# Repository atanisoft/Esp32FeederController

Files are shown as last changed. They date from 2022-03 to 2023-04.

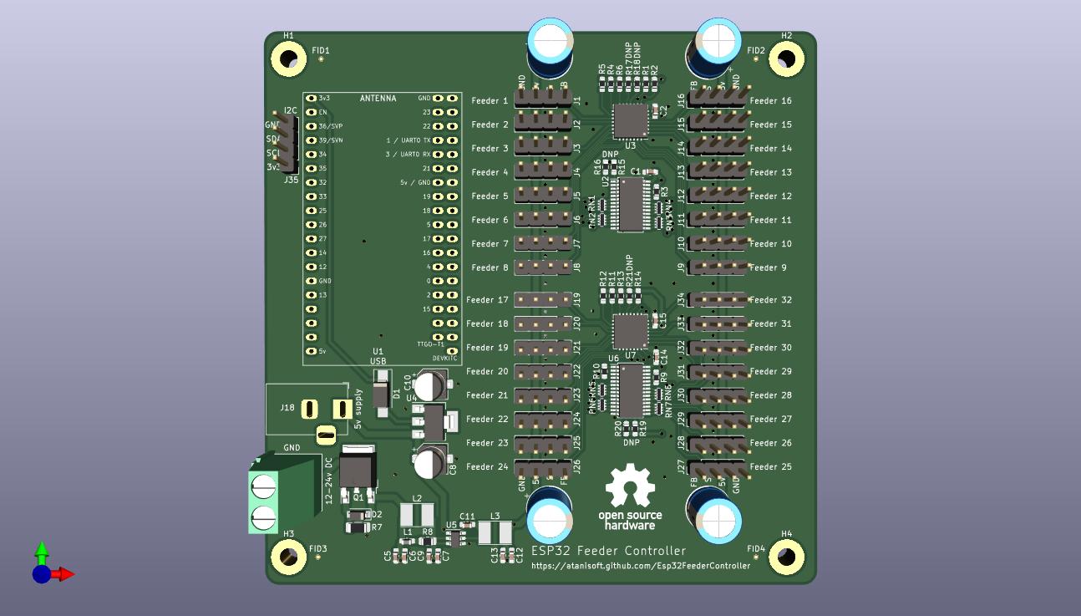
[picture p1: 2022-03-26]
pcb/FeederController.jpg

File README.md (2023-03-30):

# Esp32FeederController

The Esp32FeederController project allows controlling of multiple 0816 Feeders
using four wire cables.

## Supported Feeders

At this time the following feeder designs should work:

* [Original 0816 Feeder](https://docs.mgrl.de/maschine:pickandplace:feeder:0816feeder).
* [0816 Lumen Feeder](https://github.com/SupaCoder/0816-Lumen-SMT-Feeder-Remix).
* [Max Feeder](https://github.com/CurlyTaleGamesLLC/MAXFeederShield).

The [Max Feeder](https://github.com/CurlyTaleGamesLLC/MAXFeederShield) is the preferred
version of the feeder design as it supports adding a QR Code to the feeder that can be
used for automatic part identification.

### Feeder modifications / Addons

* [Reel holder](https://www.thingiverse.com/thing:3810696)
* [Vertical tape puller](https://github.com/SebG3D/TapePuller/wiki)

## Non-automatic feeders

* [Lumen Push/Pull Feeder](https://github.com/GatCode/LumenPPF)

# Adding Esp32FeederController to OpenPnP

Adding Esp32FeederController to OpenPnP consists of three steps:

* Create [GcodeDriver](https://github.com/openpnp/openpnp/wiki/GcodeDriver).
* Create [Actuators](https://github.com/openpnp/openpnp/wiki/Setup-and-Calibration%3A-Actuators) for Feeder actions.
* Create [Feeders](https://github.com/openpnp/openpnp/wiki/Setup-and-Calibration%3A-Feeders). 

### Creating the Gcode Driver

Each Esp32FeederController PCB should have it's own [GcodeDriver](https://github.com/openpnp/openpnp/wiki/GcodeDriver).

Steps to add a new [GcodeDriver](https://github.com/openpnp/openpnp/wiki/GcodeDriver) for Esp32FeederController:

* Navigate to the `Machine Setup` tab
* Traverse the list to the `Drivers` section, select and expand it.
* Click the `+` (add) icon and select `GcodeDriver`.
* Select the newly created `GcodeDriver GcodeDriver` entry.
* Set the `Name` so it can be easily identified later.
* Set `Communications Type` to `tcp`.
* Scroll down to the `TCP` section.
* Set `IP Address` based on the reported IP address in the serial output.
* Set `Port` to `8989`.
* Click the `Apply` button to save the updates.
* In the `File` menu select `Save Configuration` to ensure settings are not lost when restarting OpenPnP.

### Creating Actuators

Each Esp32FeederController PCB requires two `Actuators`:

* Feeder Advancement
* Feeder Post Pick

The following steps should be executed for the two `Actuators`:

* Navigate to the `Machine Setup` tab
* Traverse the list to the `Actuators` section, select and expand it.
* Click the `+` (add) icon and select `ReferenceActuator`.
* Select the newly created `ReferenceActuator ReferenceActuator` entry.
* Set `Driver` to the Esp32FeederController driver created previously.
* Set the `Name` so it can be easily identified later.
* Set `Value Type` to `Double`.
* Click the `Apply` button to save the updates.
* In the `File` menu select `Save Configuration` to ensure settings are not lost when restarting OpenPnP.

After the two `Actuators` have been defined it is necessary to configure the
Gcode commands to send for actuation, use the following steps to configure this:

* Navigate to the `Machine Setup` tab
* Traverse the list to the `Drivers` section, select and expand it.
* Click the `GcodeDriver Esp32FeederController` (or whatever name was provided previously).
* Navigate to the `Gcode` tab.
* In `Head Mountable` drop down select `Default`.
  * In `Setting` select `COMMAND_CONFIRM_REGEX` and enter `^ok.*`, be sure to click `Apply` before moving further.
  * In `Setting` select `COMMAND_ERROR_REGEX` and enter `^error.*`, be sure to click `Apply` before moving further.
* In `Head Mountable` drop down select `Actuator: [No Head] Feeder Advancement`.
  * In `Setting` select `ACTUATE_DOUBLE_COMMAND` and enter `M610 N{IntegerValue}*`, be sure to click `Apply` before moving further.
* In `Head Mountable` drop down select `Actuator: [No Head] Feeder Post Pick`.
  * In `Setting` select `ACTUATE_DOUBLE_COMMAND` and enter `M611 N{IntegerValue}*`, be sure to click `Apply` before moving further.
* In the `File` menu select `Save Configuration` to ensure settings are not lost when restarting OpenPnP.

## Configuring Feeders in OpenPnP

There are two types of feeders that will work well with Esp32FeederController:

* [ReferenceAutoFeeder](https://github.com/openpnp/openpnp/wiki/ReferenceAutoFeeder)
* [ReferenceSlotAutoFeeder](https://github.com/openpnp/openpnp/wiki/ReferenceSlotAutoFeeder)

Both operate similarly using the `Actuators` defined above.

* Navigate to the `Feeders` tab
* Click the `+` (add) icon and select `ReferenceAutoFeeder` or `ReferenceSlotAutoFeeder`.
* Select the newly created `ReferenceAutoFeeder ReferenceAutoFeeder` or `ReferenceSlotAutoFeeder ReferenceSlotAutoFeeder` entry.
* Double click on the newly created row in the `Name` column and rename it for easier identification.
* Set `Feed Actuator` to `Feeder Advancement` (or whichever name you provide the `Actuator`)
* Set `Post Pick Actuator` to `Feeder Post Pick` (or whichever name you provide the `Actuator`)
* Set `Actuator Value` on both `Actuators` to the feeder number on the Esp32FeederController PCB minus one (zero indexed).
* Click the `Apply` button to save the updates.
* In the `File` menu select `Save Configuration` to ensure settings are not lost when restarting OpenPnP.

Use the `Test Feed` and `Test post pick` to confirm the feeder is responding correctly.

## Supported Gcode commands

The Esp32FeederController supports multiple Gcode commands, many of which are
not directly used by OpenPnP. Many of the commands are intended to be used with
substitution of values within `{ }` marks, anything within `[ ]` are optional
arguments.

### Feeder Movement (M610)

`M610 N{feeder} [D{distance}]`

* `{feeder}` is the Feeder to be moved forward.
* `{distance}` is the distance to move the feeder and is optional.

### Feeder Post Pick (M611)

`M611 N{feeder}`

* `{feeder}` is the Feeder to be moved as part of post-pick.

### Feeder Status (M612)

`M612 N{feeder}`

* `{feeder}` is the Feeder to retrieve status for.

### Feeder Configuration (M613)

`M613 N{feeder} [A{advance angle}] [B{half advance angle}] [C{retract angle}] [D{degrees}] [F{feed length}] [S{speed}] [U{settle time}] [V{min pulse}] [W{max pulse}] [Z{feedback enabled}]`

All parameters except `{feeder}` are optional.

* `{feeder}` is the Feeder to be configured.
* `{advance angle}` is the angle to move the servo to for full extension.
* `{half advance angle}` is the angle to move the servo to for half extension.
* `{retract angle}` is the angle to move the servo to for retraction.
* `{degrees}` is the maximum number of degrees to move at one time, set to zero to move immediately.
* `{feed length}` is the number of millimeters (pitch) to move the feeder forward when moving to the next part and must be a multiple of 2.
* `{speed}` is the interval at which to move the servo between two angles, used in conjunction with `{degrees}`.
* `{settle time}` is the number of milliseconds to delay between servo movements.
* `{min pulse}` is the minimum number of pulses to send the servo.
* `{max pulse}` is the maximum number of pulses to send the servo.
* `{feedback enabled}` is used to enable or disable feedback checking as part of movement, set to zero to disable or one to enable

### Enable Feeder (M614)

`M614 N{feeder}`

* `{feeder}` is the Feeder to enable.

### Disable Feeder (M615)

`M615 N{feeder}`

* `{feeder}` is the Feeder to disable.

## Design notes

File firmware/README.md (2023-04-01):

# Esp32FeederController Firmware

The Esp32FeederController is built using two PCA9685 PWM generators and two
MCP23017 IO Expander ICs. The [custom PCB](../pcb/FeederController/) allows
control of up to 32 feeders with a single PCB.

## Configuring your build environment

Esp32FeederController is built using [ESP-IDF](https://github.com/espressif/esp-idf),
most testing is done with the master branch (v5.0 or later).
Please follow [these](https://docs.espressif.com/projects/esp-idf/en/latest/esp32/get-started/index.html#installation)
instructions for setting up your build environment.

## Building and flashing the firmware

Once the environment has been setup you are almost ready to build and upload the
binary to the ESP32. Before building you will need to configure your WiFi access
details in `firmware/main/config.hxx` in the `WIFI_SSID` and `WIFI_PASSWORD`
fields. Once the two WiFi fields have been updated you are ready to build.

Plug in the ESP32 to your computer and execute the following commands to build
and flash the firmware to the ESP32:

```
idf.py build flash monitor -p /dev/ttyUSB0
```

Adjust `/dev/ttyUSB0` to match the port assigned to the ESP32 when it is plugged
into your computer.

Once the firmware has been uploaded the ESP32 will restart and the serial output
will be displayed in the terminal. The startup process should take 5-10 seconds
the first time and will display the assigned IP address:

```
I (587) main: Initializing NVS
I (650) wifi_mgr: Setting hostname to "esp32feeder".
I (656) wifi_mgr: Configuring Station (SSID:YourWiFiNetwork)
I (657) wifi_mgr: Starting WiFi stack
I (756) wifi_mgr: WiFi station started.
I (1935) wifi_mgr: Connected to SSID:YourWiFiNetwork
I (1936) wifi_mgr: [1/36] Waiting for IP address assignment.
I (2104) wifi_mgr: IP address:10.0.0.13
I (2105) wifi_mgr: [2/36] Waiting for IP address assignment.
I (2114) gcode_server: Waiting for connections on 10.0.0.13:8989...
```
Make note of the IP address that is reported as you will need it for OpenPnP
configuration.

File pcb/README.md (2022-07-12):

# Custom PCBs

This tree contains custom PCBs for the Esp32FeederController. Note that this PCB
has not been extensively tested or verified to be bug-free. Please report any
issues with the PCBs and if possible a PR to correct them.

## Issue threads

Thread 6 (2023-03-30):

ESP32 abort on FeederManager.cpp

indexdb, 2023-03-30:
I use one PCA9685 and one MCP23017, ESP32 detected them, but reboot endless, please check log attached.

ESP32 abort on this line in FeederManager.cpp, then reboot ....
feeders_.push_back( std::make_shared<Feeder>(idx + 1, uuid, pca9685_[expander_index],
                                        mcp23017_[expander_index],
                                        expander_channel, context));

========================== LOG =================================
20:11:48.220 -> ELF file SHA256: 8720b8c32e64e776
20:11:48.220 ->
20:11:48.220 -> Rebooting...
20:11:48.220 -> ets Jun  8 2016 00:22:57
20:11:48.267 ->
20:11:48.267 -> rst:0xc (SW_CPU_RESET),boot:0x13 (SPI_FAST_FLASH_BOOT)
20:11:48.267 -> configsip: 0, SPIWP:0xee
20:11:48.267 -> clk_drv:0x00,q_drv:0x00,d_drv:0x00,cs0_drv:0x00,hd_drv:0x00,wp_drv:0x00
20:11:48.267 -> mode:DIO, clock div:2
20:11:48.267 -> load:0x3fff0030,len:6948
20:11:48.267 -> load:0x40078000,len:15500
20:11:48.267 -> load:0x40080400,len:3844
20:11:48.267 -> entry 0x4008064c
20:11:48.267 ->  [0;32mI (27) boot: ESP-IDF -128-NOTFOUND 2nd stage bootloader [0m
20:11:48.267 ->  [0;32mI (27) boot: compile time 16:58:17 [0m
20:11:48.267 ->  [0;32mI (27) boot: chip revision: v1.0 [0m
20:11:48.267 ->  [0;32mI (31) boot.esp32: SPI Speed      : 40MHz [0m
20:11:48.267 ->  [0;32mI (35) boot.esp32: SPI Mode       : DIO [0m
20:11:48.313 ->  [0;32mI (40) boot.esp32: SPI Flash Size : 4MB [0m
20:11:48.313 ->  [0;32mI (44) boot: Enabling RNG early entropy source... [0m
20:11:48.313 ->  [0;32mI (50) boot: Partition Table: [0m
20:11:48.313 ->  [0;32mI (53) boot: ## Label            Usage          Type ST Offset   Length [0m
20:11:48.313 ->  [0;32mI (61) boot:  0 nvs              WiFi data        01 02 00009000 00006000 [0m
20:11:48.313 ->  [0;32mI (68) boot:  1 phy_init         RF data          01 01 0000f000 00001000 [0m
20:11:48.313 ->  [0;32mI (76) boot:  2 factory          factory app      00 00 00010000 00177000 [0m
20:11:48.313 ->  [0;32mI (83) boot: End of partition table [0m
20:11:48.361 ->  [0;32mI (87) esp_image: segment 0: paddr=00010020 vaddr=3f400020 size=41804h (268292) map [0m
20:11:48.454 ->  [0;32mI (193) esp_image: segment 1: paddr=0005182c vaddr=3ffb0000 size=03638h ( 13880) load [0m
20:11:48.454 ->  [0;32mI (198) esp_image: segment 2: paddr=00054e6c vaddr=40080000 size=0b1ach ( 45484) load [0m
20:11:48.454 ->  [0;32mI (217) esp_image: segment 3: paddr=00060020 vaddr=400d0020 size=c53dch (807900) map [0m
20:11:48.735 ->  [0;32mI (509) esp_image: segment 4: paddr=00125404 vaddr=4008b1ac size=0b744h ( 46916) load [0m
20:11:48.782 ->  [0;32mI (540) boot: Loaded app from partition at offset 0x10000 [0m
20:11:48.782 ->  [0;32mI (540) boot: Disabling RNG early entropy source... [0m
20:11:48.829 ->  [0;32mI (567) main: Esp32FeederController 1 Initializing [0m
20:11:48.829 ->  [0;32mI (568) main: Compiled on Mar 28 2023 16:56:01 using IDF -128-NOTFOUND [0m
20:11:48.829 ->  [0;32mI (569) main: Running from: factory [0m
20:11:48.829 ->  [0;32mI (574) soc_info: Reset reason:software reset (CPU) (12), model:ESP32, chip revision:100, number of cores:2, embedded flash:No, embedded PSRAM: No, WiFi:Yes, IEEE 802.15.4:No, BLE:Yes, BT:Yes [0m
20:11:48.829 ->  [0;32mI (591) main: Initializing NVS [0m
20:11:48.875 ->  [0;32mI (626) wifi_mgr: Setting hostname to "esp32feeder". [0m
20:11:48.875 ->  [0;32mI (632) wifi_mgr: Configuring Station (SSID:QiQi Wifi-2.4G) [0m
20:11:48.875 ->  [0;32mI (633) wifi_mgr: Starting WiFi stack [0m
20:11:48.969 ->  [0;32mI (723) wifi_mgr: WiFi station started. [0m
20:11:49.579 -> E (1328) wifi:Association refused temporarily, comeback time 1004 mSec
20:11:50.562 -> E (2339) wifi:Association refused temporarily, comeback time 1004 mSec
20:11:51.590 ->  [0;32mI (3349) wifi_mgr: Connection to SSID:QiQi Wifi-2.4G (reason:203) failed [0m
20:11:51.636 ->  [0;32mI (3386) wifi_mgr: Connected to SSID:QiQi Wifi-2.4G [0m
20:11:51.636 ->  [0;32mI (3387) wifi_mgr: [1/36] Waiting for IP address assignment. [0m
20:11:52.622 ->  [0;32mI (4388) wifi_mgr: IP address:192.168.1.164 [0m
20:11:52.622 ->  [0;32mI (4389) wifi_mgr: [2/36] Waiting for IP address assignment. [0m
20:11:52.622 ->  [0;32mI (4397) gcode_client_mgr: 0 clients connected [0m
20:11:52.669 ->  [0;32mI (4399) gcode_server: Waiting for connections on 192.168.1.164:8989... [0m
20:11:52.669 ->  [0;32mI (4406) feeder_mgr: Initializing I2C Bus [0m
20:11:52.669 ->  [0;33mW (4408) feeder_mgr: PCA9685(40) was not detected. [0m
20:11:52.669 ->  [0;33mW (4412) feeder_mgr: PCA9685(41) was not detected. [0m
20:11:52.669 ->  [0;33mW (4418) feeder_mgr: PCA9685(42) was not detected. [0m
20:11:52.669 ->  [0;32mI (4425) feeder_mgr: PCA9685(43/0x3ffca244) configured for use. [0m
20:11:52.669 ->  [0;33mW (4430) feeder_mgr: PCA9685(44) was not detected. [0m
20:11:52.669 ->  [0;33mW (4435) feeder_mgr: PCA9685(45) was not detected. [0m
20:11:52.717 ->  [0;33mW (4441) feeder_mgr: PCA9685(46) was not detected. [0m
20:11:52.717 ->  [0;33mW (4446) feeder_mgr: PCA9685(47) was not detected. [0m
20:11:52.717 ->  [0;32mI (4451) feeder_mgr: Detected PCA9685 devices:1 [0m
20:11:52.717 ->  [0;33mW (4457) feeder_mgr: MCP23017(20) was not detected! [0m
20:11:52.717 ->  [0;33mW (4462) feeder_mgr: MCP23017(21) was not detected! [0m
20:11:52.717 ->  [0;33mW (4468) feeder_mgr: MCP23017(22) was not detected! [0m
20:11:52.717 ->  [0;32mI (4477) feeder_mgr: MCP23017(23/0x3ffca284) configured for use. [0m
20:11:52.717 ->  [0;33mW (4480) feeder_mgr: MCP23017(24) was not detected! [0m
20:11:52.717 ->  [0;33mW (4486) feeder_mgr: MCP23017(25) was not detected! [0m
20:11:52.765 ->  [0;33mW (4491) feeder_mgr: MCP23017(26) was not detected! [0m
20:11:52.765 ->  [0;33mW (4497) feeder_mgr: MCP23017(27) was not detected! [0m
20:11:52.765 ->
20:11:52.765 -> abort() was called at PC 0x4014f40f on core 0
20:11:52.765 ->
20:11:52.765 ->
20:11:52.765 -> Backtrace: 0x40081f0e:0x3ffba1c0 0x40089eed:0x3ffba1e0 0x40090f22:0x3ffba200 0x4014f40f:0x3ffba280 0x4014f444:0x3ffba2a0 0x4014f51f:0x3ffba2c0 0x400e35cb:0x3ffba2e0 0x400e0c9e:0x3ffba360 0x400dab79:0x3ffba610 0x40193669:0x3ffba7a0 0x4008d331:0x3ffba7c0
20:11:52.813 ->
20:11:52.813 ->
20:11:52.813 ->
20:11:52.813 ->

atanisoft, 2023-03-30:
Can you provide the full decode of the backtrace? Also what version of ESP-IDF did you use?
```
20:11:48.267 -> �[0;32mI (27) boot: ESP-IDF -128-NOTFOUND 2nd stage bootloader�[0m
...
20:11:48.829 -> �[0;32mI (567) main: Esp32FeederController 1 Initializing�[0m
20:11:48.829 -> �[0;32mI (568) main: Compiled on Mar 28 2023 16:56:01 using IDF -128-NOTFOUND�[0m
```
These lines normally should have the ESP-IDF version but they are showing up as an invalid version. So I'm not sure how you built this thus the questions.

indexdb, 2023-03-30:
please check new log as follow
=======================
I (27) boot: ESP-IDF v5.0.1-dirty 2nd stage bootloader
I (27) boot: compile time 09:39:36
I (27) boot: chip revision: v1.0
I (31) boot.esp32: SPI Speed      : 40MHz
I (35) boot.esp32: SPI Mode       : DIO
I (40) boot.esp32: SPI Flash Size : 4MB
I (44) boot: Enabling RNG early entropy source...
I (50) boot: Partition Table:
I (53) boot: ## Label            Usage          Type ST Offset   Length
I (61) boot:  0 nvs              WiFi data        01 02 00009000 00006000
I (68) boot:  1 phy_init         RF data          01 01 0000f000 00001000
I (76) boot:  2 factory          factory app      00 00 00010000 00177000
I (83) boot: End of partition table
I (87) esp_image: segment 0: paddr=00010020 vaddr=3f400020 size=4145ch (267356) map
I (192) esp_image: segment 1: paddr=00051484 vaddr=3ffb0000 size=03638h ( 13880) load
I (198) esp_image: segment 2: paddr=00054ac4 vaddr=40080000 size=0b554h ( 46420) load
I (217) esp_image: segment 3: paddr=00060020 vaddr=400d0020 size=c498ch (805260) map
I (508) esp_image: segment 4: paddr=001249b4 vaddr=4008b554 size=0b32ch ( 45868) load
I (539) boot: Loaded app from partition at offset 0x10000
I (539) boot: Disabling RNG early entropy source...
I (566) main: Esp32FeederController 1 Initializing
I (567) main: Compiled on Mar 30 2023 09:35:52 using IDF v5.0.1-dirty
I (568) main: Running from: factory
I (572) soc_info: Reset reason:software reset (CPU) (12), model:ESP32, chip revision:100, number of cores:2, embedded flash:No, embedded PSRAM: No, WiFi:Yes, IEEE 802.15.4:No, BLE:Yes, BT:Yes
I (590) main: Initializing NVS
I (623) wifi_mgr: Setting hostname to "esp32feeder".
I (630) wifi_mgr: Configuring Station (SSID:QiQi Wifi-2.4G)
I (630) wifi_mgr: Starting WiFi stack
I (721) wifi_mgr: WiFi station started.
I (1759) wifi_mgr: Connected to SSID:XXXXX
I (1760) wifi_mgr: [1/36] Waiting for IP address assignment.
I (1773) wifi_mgr: IP address:192.168.1.164
I (1773) wifi_mgr: [2/36] Waiting for IP address assignment.
I (1781) gcode_client_mgr: 0 clients connected
I (1782) gcode_server: Waiting for connections on 192.168.1.164:8989...
I (1790) feeder_mgr: Initializing I2C Bus
W (1792) feeder_mgr: PCA9685(40) was not detected.
W (1796) feeder_mgr: PCA9685(41) was not detected.
W (1802) feeder_mgr: PCA9685(42) was not detected.
I (1809) feeder_mgr: PCA9685(43/0x3ffca198) configured for use.
W (1814) feeder_mgr: PCA9685(44) was not detected.
W (1819) feeder_mgr: PCA9685(45) was not detected.
W (1825) feeder_mgr: PCA9685(46) was not detected.
W (1830) feeder_mgr: PCA9685(47) was not detected.
I (1838) feeder_mgr: Detected PCA9685 devices:1
W (1841) feeder_mgr: MCP23017(20) was not detected!
W (1847) feeder_mgr: MCP23017(21) was not detected!
W (1853) feeder_mgr: MCP23017(22) was not detected!
I (1861) feeder_mgr: MCP23017(23/0x3ffca1d8) configured for use.
W (1864) feeder_mgr: MCP23017(24) was not detected!
W (1870) feeder_mgr: MCP23017(25) was not detected!
W (1875) feeder_mgr: MCP23017(26) was not detected!
W (1881) feeder_mgr: MCP23017(27) was not detected!

abort() was called at PC 0x4014eab3 on core 0
0x4014eab3: __cxxabiv1::__terminate(void (*)()) at /builds/idf/crosstool-NG/.build/HOST-x86_64-w64-mingw32/xtensa-esp32-elf/src/gcc/libstdc++-v3/libsupc++/eh_terminate.cc:48
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
atanisoft, 2023-03-30:
Thanks for reproducing it on IDF v4.4. This was working previously and was tested, something must have changed in the gcc versions or IDF since I last tested this.

I'm working on adding some additional logging and support fixes for IDF v5+. Did you see this sort of failure in your testing?
```
xtensa-esp32-elf/bin/ld: esp-idf/espressif__asio/libespressif__asio.a(asio.cpp.obj):(.literal._ZN4asio6detail10socket_ops9inet_ntopEiPKvPcjmRSt10error_code+0x8): undefined reference to `if_indextoname'
xtensa-esp32-elf/bin/ld: esp-idf/espressif__asio/libespressif__asio.a(asio.cpp.obj): in function `_ZN4asio6detail10socket_ops9inet_ntopEiPKvPcjmRSt10error_code':
Esp32FeederController/firmware/managed_components/espressif__asio/asio/asio/include/asio/detail/impl/socket_ops.ipp:2128: undefined reference to `if_indextoname'
collect2: error: ld returned 1 exit status
```

indexdb, 2023-03-30:
Yes，I see that failure and I fix it by adding
----------------------------------------------------------
char* if_indextoname(unsigned int , char* ) { return 0; }
----------------------------------------------------------
to file socket_ops.ipp

You can check the link for this issue
https://github.com/espressif/esp-idf/issues/3557

atanisoft, 2023-03-30:
That was fixed and should have been included in the latest IDF but something is broken on asio it seems still. I saw a PR adding a missing header reference for the same thing. I'll be adding the weak function definition as referenced from that issue in my update.

atanisoft, 2023-03-30:
@indexdb Can you test the code on "idfv5" branch? It should compile cleanly without needing to alter anything with IDF v5.0.x

indexdb, 2023-03-30:
Yes, it works， Thank you！

Closed 2023-03-30.

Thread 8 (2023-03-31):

GCode command return nothing

indexdb, 2023-03-31:
I try to send Gcode command （ex. M115）from openpnp gcode driver console，got nothing.
Sometimes it returns "ok", most of the time it returns nothing
-----------------------------------------------------------------------
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
ok
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
-----------------------------------------------------------------------------
I (27) boot: ESP-IDF v5.0.1-dirty 2nd stage bootloader
I (27) boot: compile time 19:27:32
I (27) boot: chip revision: v1.0
I (30) boot.esp32: SPI Speed      : 40MHz
I (35) boot.esp32: SPI Mode       : DIO
I (39) boot.esp32: SPI Flash Size : 4MB
I (44) boot: Enabling RNG early entropy source...
I (49) boot: Partition Table:
I (53) boot: ## Label            Usage          Type ST Offset   Length
I (60) boot:  0 nvs              WiFi data        01 02 00009000 00006000
I (68) boot:  1 phy_init         RF data          01 01 0000f000 00001000
I (75) boot:  2 factory          factory app      00 00 00010000 00177000
I (83) boot: End of partition table
I (87) esp_image: segment 0: paddr=00010020 vaddr=3f400020 size=4163ch (267836) map
I (192) esp_image: segment 1: paddr=00051664 vaddr=3ffb0000 size=03638h ( 13880) load
I (198) esp_image: segment 2: paddr=00054ca4 vaddr=40080000 size=0b374h ( 45940) load
I (217) esp_image: segment 3: paddr=00060020 vaddr=400d0020 size=c4b88h (805768) map
I (508) esp_image: segment 4: paddr=00124bb0 vaddr=4008b374 size=0b50ch ( 46348) load
I (539) boot: Loaded app from partition at offset 0x10000
I (539) boot: Disabling RNG early entropy source...
I (566) main: Esp32FeederController 1 Initializing
I (567) main: Compiled on Mar 31 2023 19:23:37 using IDF v5.0.1-dirty
I (568) main: Running from: factory
I (572) soc_info: Reset reason:power on reset (1), model:ESP32, chip revision:100, number of cores:2, embedded flash:No, embedded PSRAM: No, WiFi:Yes, IEEE 802.15.4:No, BLE:Yes, BT:Yes
I (590) main: Initializing NVS
I (623) wifi_mgr: Setting hostname to "esp32feeder".
I (630) wifi_mgr: Configuring Station (SSID: Wifi-2.4G)
I (630) wifi_mgr: Starting WiFi stack
I (720) wifi_mgr: WiFi station started.
I (1971) wifi_mgr: Connected to SSID: Wifi-2.4G
I (1972) wifi_mgr: [1/36] Waiting for IP address assignment.
I (1996) wifi_mgr: IP address:192.168.1.164
I (1997) wifi_mgr: [2/36] Waiting for IP address assignment.
I (2004) gcode_client_mgr: 0 clients connected
I (2005) gcode_server: Waiting for connections on 192.168.1.164:8989...
I (2013) feeder_mgr: Initializing I2C Bus
W (2015) feeder_mgr: PCA9685(40) was not detected.
W (2019) feeder_mgr: PCA9685(41) was not detected.
W (2025) feeder_mgr: PCA9685(42) was not detected.
I (2032) feeder_mgr: PCA9685(43/0x3ffca198) configured for use.
W (2037) feeder_mgr: PCA9685(44) was not detected.
W (2042) feeder_mgr: PCA9685(45) was not detected.
W (2048) feeder_mgr: PCA9685(46) was not detected.
W (2053) feeder_mgr: PCA9685(47) was not detected.
I (2059) feeder_mgr: Detected PCA9685 devices:1
W (2064) feeder_mgr: MCP23017(20) was not detected!
W (2070) feeder_mgr: MCP23017(21) was not detected!
W (2076) feeder_mgr: MCP23017(22) was not detected!
I (2085) feeder_mgr: MCP23017(23/0x3ffca1d8) configured for use.
W (2088) feeder_mgr: MCP23017(24) was not detected!
W (2093) feeder_mgr: MCP23017(25) was not detected!
W (2099) feeder_mgr: MCP23017(26) was not detected!
W (2104) feeder_mgr: MCP23017(27) was not detected!
I (2109) feeder_mgr: Attempting to create 16 feeders
I (2115) feeder_mgr: Detected 1 PCA9685 and 1 MCP23017
I (2121) feeder_mgr: Creating feeder A593131F (1/0/0/PCA:0x3ffca198/MCP:0x3ffca1d8)
I (2131) feeder: [A593131F:1] Initializing using PCA9685 0x3ffca198:0
I (2136) PCA9685: [43:0] Moving to 15 deg
I (2142) feeder_mgr: Enabling feeder A593131F (1)
I (2147) feeder_mgr: Creating feeder 97F4FAD4 (2/0/1/PCA:0x3ffca198/MCP:0x3ffca1d8)
I (2156) feeder: [97F4FAD4:2] Initializing using PCA9685 0x3ffca198:1
I (2162) PCA9685: [43:1] Moving to 15 deg
I (2168) feeder_mgr: Enabling feeder 97F4FAD4 (2)
I (2172) feeder_mgr: Creating feeder 0E638528 (3/0/2/PCA:0x3ffca198/MCP:0x3ffca1d8)
I (2183) feeder: [0E638528:3] Initializing using PCA9685 0x3ffca198:2
I (2187) PCA9685: [43:2] Moving to 15 deg
I (2193) feeder_mgr: Enabling feeder 0E638528 (3)
I (2198) feeder_mgr: Creating feeder D3C5EB5D (4/0/3/PCA:0x3ffca198/MCP:0x3ffca1d8)
I (2207) feeder: [D3C5EB5D:4] Initializing using PCA9685 0x3ffca198:3
I (2213) PCA9685: [43:3] Moving to 15 deg
I (2219) feeder_mgr: Enabling feeder D3C5EB5D (4)
I (2223) feeder_mgr: Creating feeder 775C7838 (5/0/4/PCA:0x3ffca198/MCP:0x3ffca1d8)
I (2233) feeder: [775C7838:5] Initializing using PCA9685 0x3ffca198:4
I (2238) PCA9685: [43:4] Moving to 15 deg
I (2244) feeder_mgr: Enabling feeder 775C7838 (5)
I (2249) feeder_mgr: Creating feeder 660C64E1 (6/0/5/PCA:0x3ffca198/MCP:0x3ffca1d8)
I (2258) feeder: [660C64E1:6] Initializing using PCA9685 0x3ffca198:5
I (2264) PCA9685: [43:5] Moving to 15 deg
I (2270) feeder_mgr: Enabling feeder 660C64E1 (6)
I (2274) feeder_mgr: Creating feeder 6134C54A (7/0/6/PCA:0x3ffca198/MCP:0x3ffca1d8)
I (2284) feeder: [6134C54A:7] Initializing using PCA9685 0x3ffca198:6
I (2290) PCA9685: [43:6] Moving to 15 deg
I (2296) feeder_mgr: Enabling feeder 6134C54A (7)
I (2300) feeder_mgr: Creating feeder D037A224 (8/0/7/PCA:0x3ffca198/MCP:0x3ffca1d8)
I (2310) feeder: [D037A224:8] Initializing using PCA9685 0x3ffca198:7
I (2315) PCA9685: [43:7] Moving to 15 deg
I (2321) feeder_mgr: Enabling feeder D037A224 (8)
I (2325) feeder_mgr: Creating feeder E351A565 (9/0/8/PCA:0x3ffca198/MCP:0x3ffca1d8)
I (2335) feeder: [E351A565:9] Initializing using PCA9685 0x3ffca198:8
I (2341) PCA9685: [43:8] Moving to 15 deg
I (2346) feeder_mgr: Enabling feeder E351A565 (9)
I (2351) feeder_mgr: Creating feeder AF13AC02 (10/0/9/PCA:0x3ffca198/MCP:0x3ffca1d8)
I (2360) feeder: [AF13AC02:10] Initializing using PCA9685 0x3ffca198:9
I (2366) PCA9685: [43:9] Moving to 15 deg
I (2372) feeder_mgr: Enabling feeder AF13AC02 (10)
I (2376) feeder_mgr: Creating feeder C06BE9EC (11/0/10/PCA:0x3ffca198/MCP:0x3ffca1d8)
I (2388) feeder: [C06BE9EC:11] Initializing using PCA9685 0x3ffca198:10
I (2392) PCA9685: [43:10] Moving to 15 deg
I (2398) feeder_mgr: Enabling feeder C06BE9EC (11)
I (2402) feeder_mgr: Creating feeder 97FBF52B (12/0/11/PCA:0x3ffca198/MCP:0x3ffca1d8)
I (2413) feeder: [97FBF52B:12] Initializing using PCA9685 0x3ffca198:11
I (2418) PCA9685: [43:11] Moving to 15 deg
I (2424) feeder_mgr: Enabling feeder 97FBF52B (12)
I (2428) feeder_mgr: Creating feeder 67703760 (13/0/12/PCA:0x3ffca198/MCP:0x3ffca1d8)
I (2438) feeder: [67703760:13] Initializing using PCA9685 0x3ffca198:12
I (2444) PCA9685: [43:12] Moving to 15 deg
I (2450) feeder_mgr: Enabling feeder 67703760 (13)
I (2455) feeder_mgr: Creating feeder E8631392 (14/0/13/PCA:0x3ffca198/MCP:0x3ffca1d8)
I (2464) feeder: [E8631392:14] Initializing using PCA9685 0x3ffca198:13
I (2470) PCA9685: [43:13] Moving to 15 deg
I (2476) feeder_mgr: Enabling feeder E8631392 (14)
I (2481) feeder_mgr: Creating feeder E838AF2F (15/0/14/PCA:0x3ffca198/MCP:0x3ffca1d8)
I (2491) feeder: [E838AF2F:15] Initializing using PCA9685 0x3ffca198:14
I (2496) PCA9685: [43:14] Moving to 15 deg
I (2502) feeder_mgr: Enabling feeder E838AF2F (15)
I (2507) feeder_mgr: Creating feeder 5CB0F53D (16/0/15/PCA:0x3ffca198/MCP:0x3ffca1d8)
I (2517) feeder: [5CB0F53D:16] Initializing using PCA9685 0x3ffca198:15
I (2522) PCA9685: [43:15] Moving to 15 deg
I (2528) feeder_mgr: Enabling feeder 5CB0F53D (16)
I (2533) feeder_mgr: Configured Feeders:16
I (2538) heap_mon: Heap: 241.09kB / 328.48kB
I (2543) main: Creating 4 worker threads
I (2551) feeder: [A593131F:1] Feeder movement complete, turning off servo
I (2551) feeder: [97F4FAD4:2] Feeder movement complete, turning off servo
I (2551) feeder: [0E638528:3] Feeder movement complete, turning off servo
I (2552) feeder: [D3C5EB5D:4] Feeder movement complete, turning off servo
I (2556) feeder: [775C7838:5] Feeder movement complete, turning off servo
I (2564) feeder: [660C64E1:6] Feeder movement complete, turning off servo
I (2570) feeder: [6134C54A:7] Feeder movement complete, turning off servo
I (2581) feeder: [D037A224:8] Feeder movement complete, turning off servo
I (2588) feeder: [E351A565:9] Feeder movement complete, turning off servo
I (2614) feeder: [AF13AC02:10] Feeder movement complete, turning off servo
I (2552) main: Esp32FeederController Ready!
I (2640) feeder: [C06BE9EC:11] Feeder movement complete, turning off servo
I (2665) feeder: [97FBF52B:12] Feeder movement complete, turning off servo
I (2692) feeder: [67703760:13] Feeder movement complete, turning off servo
I (2718) feeder: [E8631392:14] Feeder movement complete, turning off servo
I (2743) feeder: [E838AF2F:15] Feeder movement complete, turning off servo
I (2769) feeder: [5CB0F53D:16] Feeder movement complete, turning off servo
I (32006) gcode_client_mgr: 0 clients connected
I (32544) heap_mon: Heap: 222.73kB / 328.48kB
I (62009) gcode_client_mgr: 0 clients connected
I (62316) gcode_server: New client:192.168.1.123
I (62549) heap_mon: Heap: 220.05kB / 328.48kB
I (82381) gcode_client: [192.168.1.123] Command:M115
I (86889) gcode_client: [192.168.1.123] Command:M115
I (89963) gcode_client: [192.168.1.123] Command:M115
I (91507) gcode_client: [192.168.1.123] Command:M115
I (92012) gcode_client_mgr: 1 clients connected
I (92318) gcode_client: [192.168.1.123] Command:M115
I (92553) heap_mon: Heap: 219.27kB / 328.48kB
I (94880) gcode_client: [192.168.1.123] Command:M115
I (105227) gcode_client: [192.168.1.123] Command:M612
I (105228) feeder_mgr: feeder status request received
I (122015) gcode_client_mgr: 1 clients connected
I (122557) heap_mon: Heap: 219.40kB / 328.48kB
I (128266) gcode_client: [192.168.1.123] Command:M612
I (128267) feeder_mgr: feeder status request received
I (140553) gcode_client: [192.168.1.123] Command:M115
I (140571) gcode_client: [192.168.1.123] Command:M114
I (152018) gcode_client_mgr: 1 clients connected
I (152562) heap_mon: Heap: 219.04kB / 328.48kB
I (172413) gcode_client: [192.168.1.123] Command:M115
I (174869) gcode_client: [192.168.1.123] Command:M115
I (182021) gcode_client_mgr: 1 clients connected
I (182567) heap_mon: Heap: 219.04kB / 328.48kB
I (212024) gcode_client_mgr: 1 clients connected
I (212570) heap_mon: Heap: 219.13kB / 328.48kB
I (216861) gcode_client: [192.168.1.123] Command:M115
I (242027) gcode_client_mgr: 1 clients connected
I (242573) heap_mon: Heap: 217.38kB / 328.48kB
I (272029) gcode_client_mgr: 1 clients connected
I (272579) heap_mon: Heap: 218.77kB / 328.48kB

atanisoft, 2023-04-01:
Did you test this from OpenPnP or another client connecting to the endpoint? The M115 command should be returning text, it doesn't print anything on the console when it does though.

indexdb, 2023-04-01:
yes, I  send geode from openpnp console and telnet

indexdb, 2023-04-01:
I checkout the main code, It works. Maybe I use the branch code not main before.

Closed 2023-04-01.

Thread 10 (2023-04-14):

Servo doesn't work

indexdb, 2023-04-14:
I assembled Max feeder, N20 motro is work, but the Servo doesn't work, I have test the servo, it's good.
everything seem good, but Servo do nothing. I wonder if you test the servo after last bug fixed.

I (4348) feeder_mgr: Initializing I2C Bus
W (4350) feeder_mgr: PCA9685(40) was not detected.
W (4354) feeder_mgr: PCA9685(41) was not detected.
W (4360) feeder_mgr: PCA9685(42) was not detected.
I (4367) feeder_mgr: PCA9685(43/0x3ffca1a8) configured for use.
W (4372) feeder_mgr: PCA9685(44) was not detected.
W (4377) feeder_mgr: PCA9685(45) was not detected.
W (4383) feeder_mgr: PCA9685(46) was not detected.
W (4388) feeder_mgr: PCA9685(47) was not detected.
I (4396) feeder_mgr: Detected PCA9685 devices:1
W (4399) feeder_mgr: MCP23017(20) was not detected!
W (4404) feeder_mgr: MCP23017(21) was not detected!
W (4411) feeder_mgr: MCP23017(22) was not detected!
I (4419) feeder_mgr: MCP23017(23/0x3ffca1e8) configured for use.
W (4422) feeder_mgr: MCP23017(24) was not detected!
W (4428) feeder_mgr: MCP23017(25) was not detected!
W (4433) feeder_mgr: MCP23017(26) was not detected!
W (4439) feeder_mgr: MCP23017(27) was not detected!
I (4444) feeder_mgr: Attempting to create 16 feeders
I (4450) feeder_mgr: Detected 1 PCA9685 and 1 MCP23017
I (4456) feeder_mgr: Creating feeder BA061284 (0/0/0/PCA:0x3ffca1a8/MCP:0x3ffca1e8)
I (4466) feeder: [BA061284:0] Initializing using PCA9685 0x3ffca1a8:0
I (4471) feeder: [BA061284:0] Subscribing to MCP23017 channel 0
I (4478) feeder: [BA061284:0] Feedback enabled using MCP23017 0x3ffca1e8:0
--------------------------------------------------------------------------------------

I (116263) PCA9685: [43:0] Moving to 90 deg
I (116511) feeder: [BA061284:0] Feeder movement complete, turning off servo
I (117223) feeder: [BA061284:0] Feeder fully advanced, retracting
I (117224) PCA9685: [43:0] Moving to 15 deg
I (117467) feeder: [BA061284:0] Feeder movement remaining: 4mm
I (117468) feeder: [BA061284:0] Feeder is retracted
I (117469) feeder: [BA061284:0] Moving to fully advanced position
I (117476) PCA9685: [43:0] Moving to 90 deg
I (117723) feeder: [BA061284:0] Feeder movement complete, turning off servo
I (117912) feeder: [BA061284:0] Feeder fully advanced, retracting
I (117913) PCA9685: [43:0] Moving to 15 deg
I (118156) feeder: [BA061284:0] Feeder movement remaining: 4mm
I (118157) feeder: [BA061284:0] Feeder is retracted
I (118158) feeder: [BA061284:0] Moving to fully advanced position
I (118165) PCA9685: [43:0] Moving to 90 deg
I (118413) feeder: [BA061284:0] Feeder movement complete, turning off servo
I (118702) feeder: [BA061284:0] Feeder fully advanced, retracting
I (118703) PCA9685: [43:0] Moving to 15 deg
I (118946) feeder: [BA061284:0] Feeder movement remaining: 4mm
I (118947) feeder: [BA061284:0] Feeder is retracted
I (118948) feeder: [BA061284:0] Moving to fully advanced position
I (118954) PCA9685: [43:0] Moving to 90 deg

atanisoft, 2023-04-15:
Did you provide a 5v power to the PCA9685 board? Did the servo move (or make noise) during startup?

indexdb, 2023-04-15:
of course, +5v is provided to servo, no move no noise anytime.

atanisoft, 2023-04-15:
Ok, will see if I can reproduce it locally.

indexdb, 2023-04-15:
I will use oscilloscope to check the pwm signal tomorrow.

indexdb, 2023-04-15:
I use logic analyzer to check S pin, no signal is captured, I resolder PCA9685, the problem is still the same, servo has no action and noise.

indexdb, 2023-04-15:
I found the solution.
This bug is caused by a wrong design of pcb, 23 pin of PCA9685   /OE is low enable. But your circuit diagram connects to 3.3v via 10k resistor, which causes the output to be disabled. The solution is to remove R3 and R9, and will work fine.

atanisoft, 2023-04-15:
ahh, good find. I somehow didn't see this in my tests. I'll update the PCB to list those as DNP.

indexdb, 2023-04-16:
I found another issue, the PCA9685 address a0 a1 is connected to high, but a2 a3 a4 a5 is not connected, leading to a random address sometimes instead of 0x43 during i2c scan.
a2 a3 a4 a5 should be properly grounded. Also, the MCP23017 has the same grounding issue, but no problem was found in the actual test. However, I found the MCP23017 connected to the same address on the schematic, i.e. a0 a1 connected to high, a2 not connected.

Closed 2023-04-16.

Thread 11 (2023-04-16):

PCA9685 and MCP23017 address issue

indexdb, 2023-04-16:
I found another issue, the PCA9685 address a0 a1 is connected to high, but a2 a3 a4 a5 is not connected, leading to a random address sometimes instead of 0x43 during i2c scan.
a2 a3 a4 a5 should be properly grounded. Also, the MCP23017 has the same grounding issue, but no problem was found in the actual test. However, I found the MCP23017 connected to the same address on the schematic, i.e. a0 a1 connected to high, a2 not connected.

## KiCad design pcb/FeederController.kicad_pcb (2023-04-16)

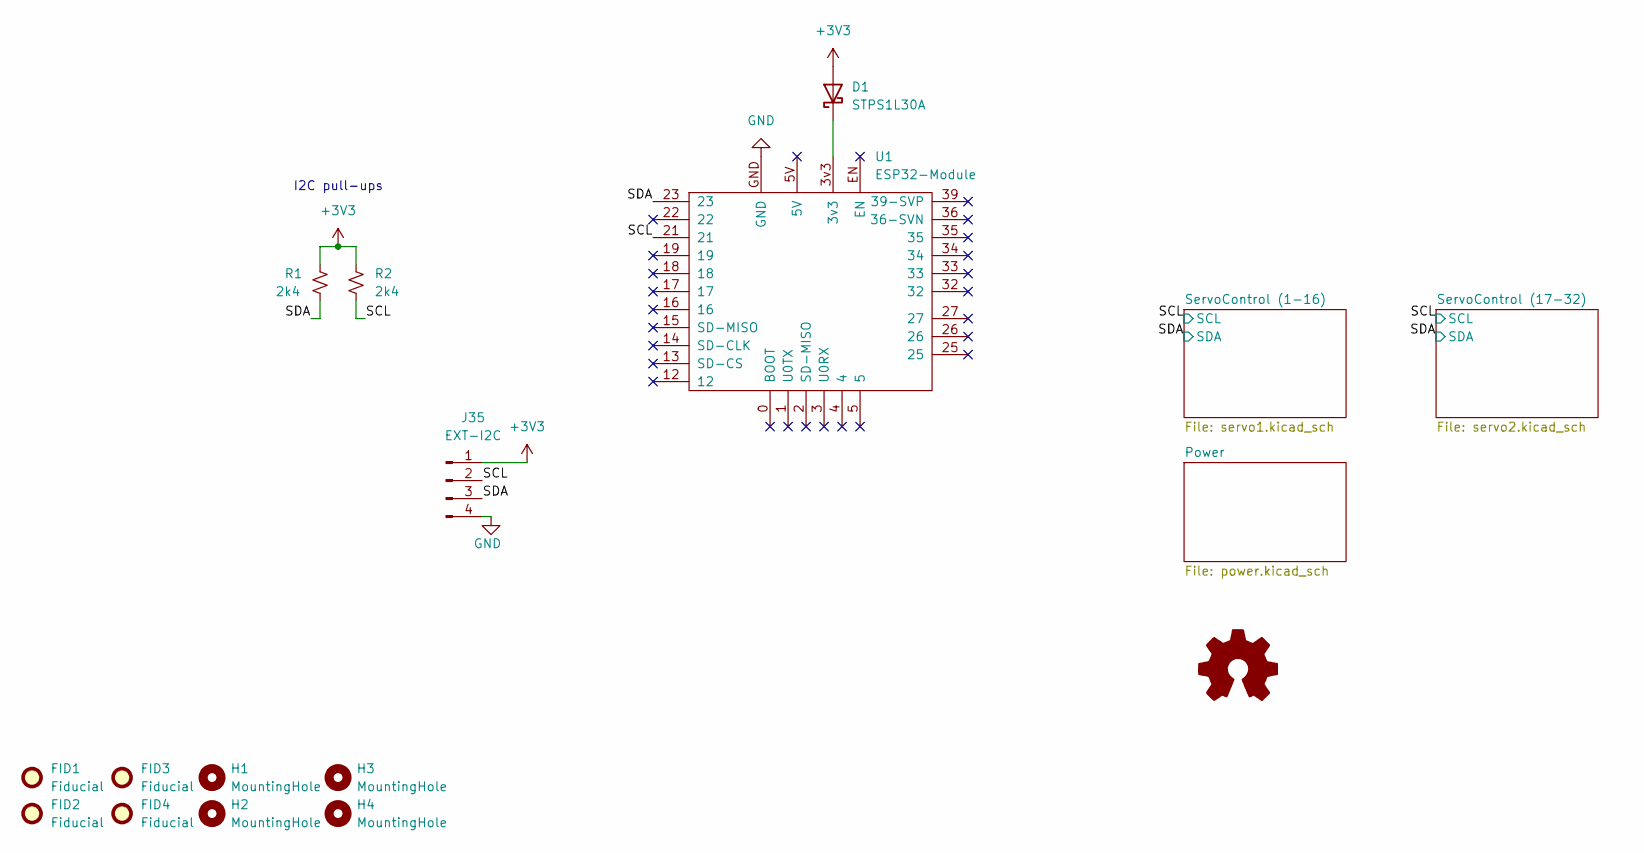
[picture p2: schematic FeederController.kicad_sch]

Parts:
D1: STPS1L30A; D_SMA_Handsoldering; Mouser 511-STPS1L30AFN
FID1, FID2, FID3, FID4: Fiducial; Fiducial_0.5mm_Mask1mm
H1, H2, H3, H4: MountingHole; MountingHole_3.2mm_M3_Pad
J35: EXT-I2C; PinHeader_1x04_P2.54mm_Vertical
R1, R2: 2k4; R_0603_1608Metric_Pad0.98x0.95mm_HandSolder
U1: ESP32-Module; TTGO-T1-DEVKIT-C

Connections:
+3V3: D1.2 (A), J35.1, R1.1, R2.1; also elsewhere on the board
/SCL: J35.2, R2.2, U1.21; also elsewhere on the board
/SDA: J35.3, R1.2, U1.23; also elsewhere on the board
GND: J35.4, U1.GND; also elsewhere on the board
unnamed: D1.1 (K), U1.3v3

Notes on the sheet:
I2C pull-ups

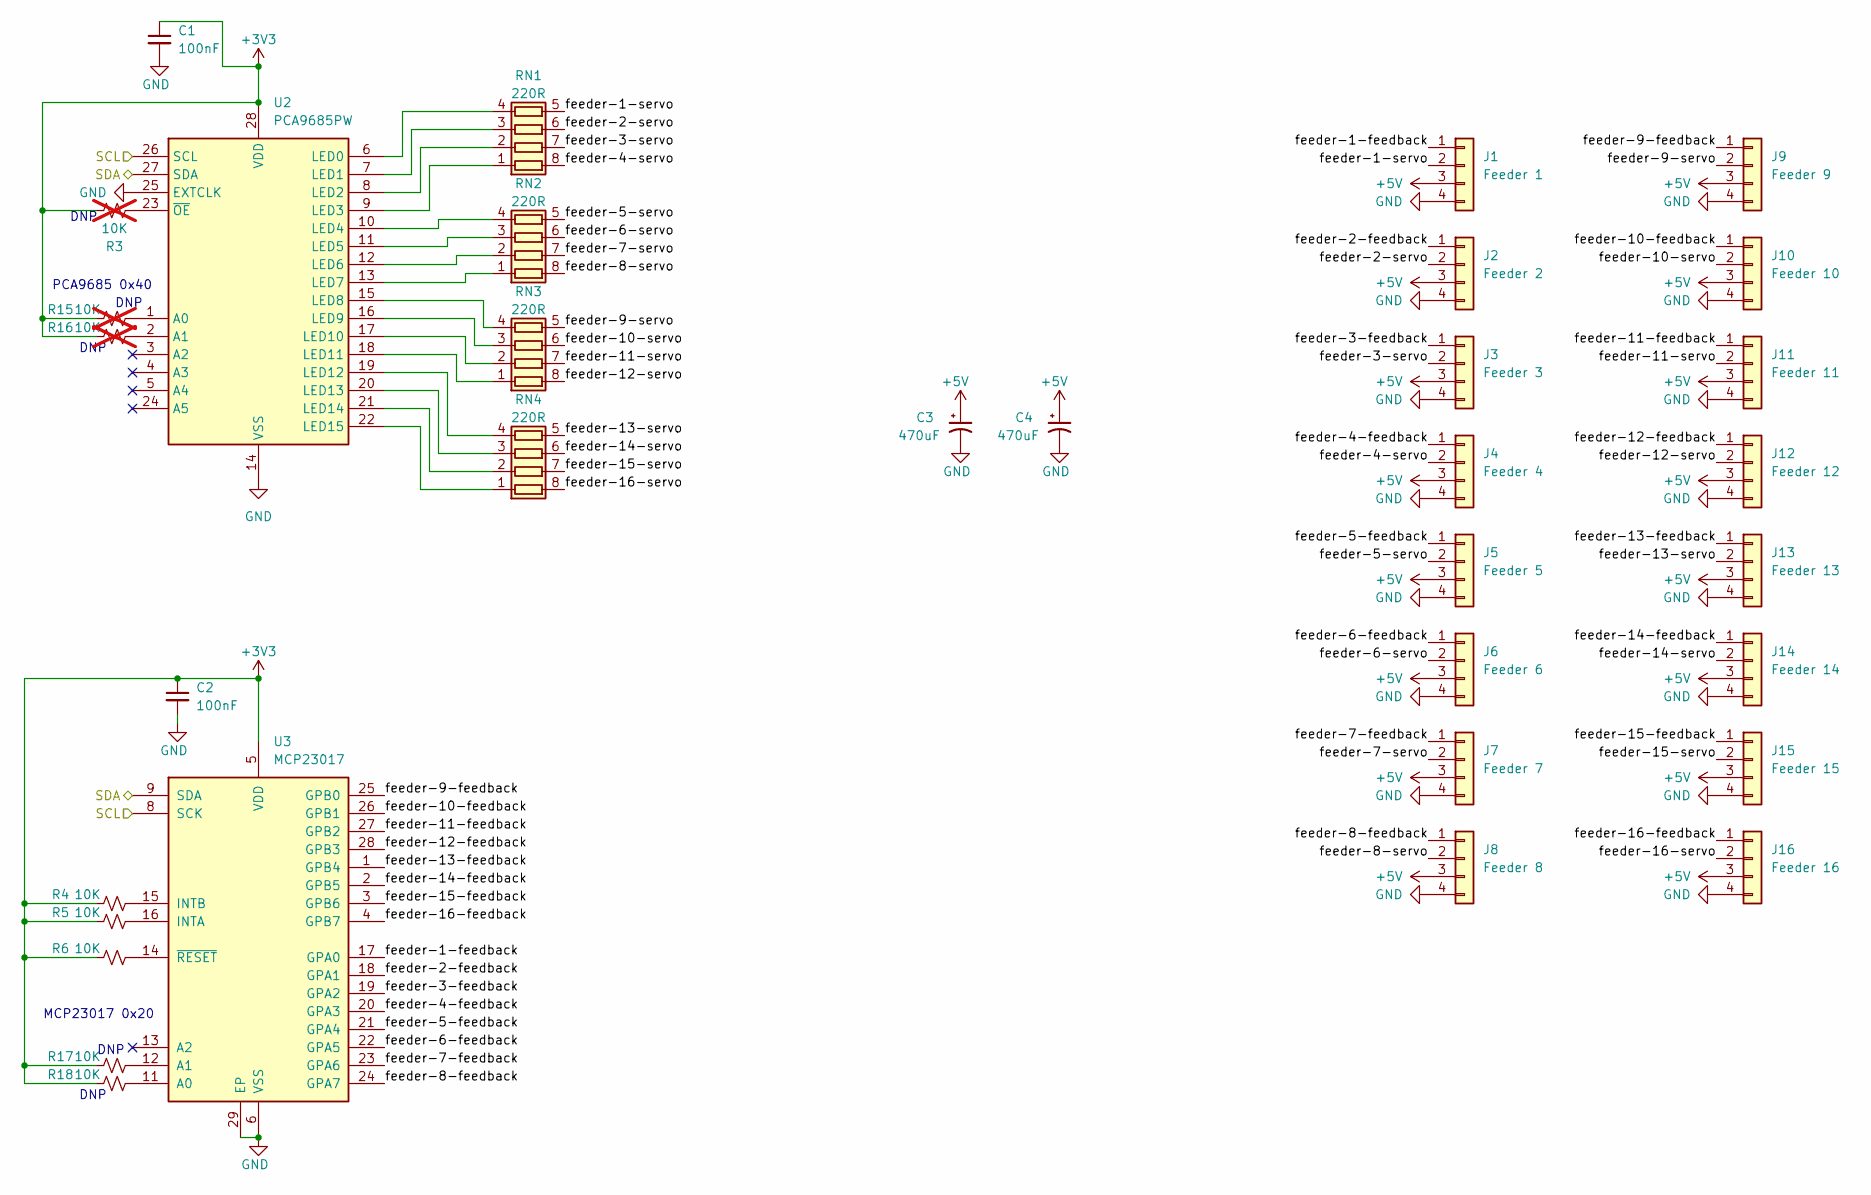
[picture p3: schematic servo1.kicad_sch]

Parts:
C1, C2: 100nF; C_0603_1608Metric_Pad1.08x0.95mm_HandSolder; Mouser 791-0603B822K250CT
C3, C4: 470uF; CP_Radial_D8.0mm_P5.00mm
J1: Feeder 1; PinHeader_1x04_P2.54mm_Vertical
J2: Feeder 2; PinHeader_1x04_P2.54mm_Vertical
J3: Feeder 3; PinHeader_1x04_P2.54mm_Vertical
J4: Feeder 4; PinHeader_1x04_P2.54mm_Vertical
J5: Feeder 5; PinHeader_1x04_P2.54mm_Vertical
J6: Feeder 6; PinHeader_1x04_P2.54mm_Vertical
J7: Feeder 7; PinHeader_1x04_P2.54mm_Vertical
J8: Feeder 8; PinHeader_1x04_P2.54mm_Vertical
J9: Feeder 9; PinHeader_1x04_P2.54mm_Vertical
J10: Feeder 10; PinHeader_1x04_P2.54mm_Vertical
J11: Feeder 11; PinHeader_1x04_P2.54mm_Vertical
J12: Feeder 12; PinHeader_1x04_P2.54mm_Vertical
J13: Feeder 13; PinHeader_1x04_P2.54mm_Vertical
J14: Feeder 14; PinHeader_1x04_P2.54mm_Vertical
J15: Feeder 15; PinHeader_1x04_P2.54mm_Vertical
J16: Feeder 16; PinHeader_1x04_P2.54mm_Vertical
R3, R15, R16: 10K; R_0603_1608Metric_Pad0.98x0.95mm_HandSolder; Mouser 279-CRGCQ0603F10K; not fitted
R4, R5, R6, R17, R18: 10K; R_0603_1608Metric_Pad0.98x0.95mm_HandSolder; Mouser 279-CRGCQ0603F10K
RN1, RN2, RN3, RN4: 220R; R_Array_Concave_4x0402
U2: PCA9685PW; TSSOP-28_4.4x9.7mm_P0.65mm
U3: MCP23017; QFN-28-1EP_6x6mm_P0.65mm_EP4.25x4.25mm

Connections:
+3V3: C1.1, C2.1, R3.1, R4.1, R5.1, R6.1, R15.1, R16.1, R17.1, R18.1, U2.28 (VDD), U3.5 (VDD); also elsewhere on the board
+5V: C3.1, C4.1, J1.3, J2.3, J3.3, J4.3, J5.3, J6.3, J7.3, J8.3, J9.3, J10.3, J11.3, J12.3, J13.3, J14.3, J15.3, J16.3; also elsewhere on the board
/SCL: U2.26 (SCL), U3.8 (SCK); also elsewhere on the board
/SDA: U2.27 (SDA), U3.9 (SDA); also elsewhere on the board
/ServoControl (1-16)/feeder-1-feedback: J1.1, U3.17 (GPA0)
/ServoControl (1-16)/feeder-1-servo: J1.2, RN1.5 (R4.2)
/ServoControl (1-16)/feeder-2-feedback: J2.1, U3.18 (GPA1)
/ServoControl (1-16)/feeder-2-servo: J2.2, RN1.6 (R3.2)
/ServoControl (1-16)/feeder-3-feedback: J3.1, U3.19 (GPA2)
/ServoControl (1-16)/feeder-3-servo: J3.2, RN1.7 (R2.2)
/ServoControl (1-16)/feeder-4-feedback: J4.1, U3.20 (GPA3)
/ServoControl (1-16)/feeder-4-servo: J4.2, RN1.8 (R1.2)
/ServoControl (1-16)/feeder-5-feedback: J5.1, U3.21 (GPA4)
/ServoControl (1-16)/feeder-5-servo: J5.2, RN2.5 (R4.2)
/ServoControl (1-16)/feeder-6-feedback: J6.1, U3.22 (GPA5)
/ServoControl (1-16)/feeder-6-servo: J6.2, RN2.6 (R3.2)
/ServoControl (1-16)/feeder-7-feedback: J7.1, U3.23 (GPA6)
/ServoControl (1-16)/feeder-7-servo: J7.2, RN2.7 (R2.2)
/ServoControl (1-16)/feeder-8-feedback: J8.1, U3.24 (GPA7)
/ServoControl (1-16)/feeder-8-servo: J8.2, RN2.8 (R1.2)
/ServoControl (1-16)/feeder-9-feedback: J9.1, U3.25 (GPB0)
/ServoControl (1-16)/feeder-9-servo: J9.2, RN3.5 (R4.2)
/ServoControl (1-16)/feeder-10-feedback: J10.1, U3.26 (GPB1)
/ServoControl (1-16)/feeder-10-servo: J10.2, RN3.6 (R3.2)
/ServoControl (1-16)/feeder-11-feedback: J11.1, U3.27 (GPB2)
/ServoControl (1-16)/feeder-11-servo: J11.2, RN3.7 (R2.2)
/ServoControl (1-16)/feeder-12-feedback: J12.1, U3.28 (GPB3)
/ServoControl (1-16)/feeder-12-servo: J12.2, RN3.8 (R1.2)
/ServoControl (1-16)/feeder-13-feedback: J13.1, U3.1 (GPB4)
/ServoControl (1-16)/feeder-13-servo: J13.2, RN4.5 (R4.2)
/ServoControl (1-16)/feeder-14-feedback: J14.1, U3.2 (GPB5)
/ServoControl (1-16)/feeder-14-servo: J14.2, RN4.6 (R3.2)
/ServoControl (1-16)/feeder-15-feedback: J15.1, U3.3 (GPB6)
/ServoControl (1-16)/feeder-15-servo: J15.2, RN4.7 (R2.2)
/ServoControl (1-16)/feeder-16-feedback: J16.1, U3.4 (GPB7)
/ServoControl (1-16)/feeder-16-servo: J16.2, RN4.8 (R1.2)
GND: C1.2, C2.2, C3.2, C4.2, J1.4, J2.4, J3.4, J4.4, J5.4, J6.4, J7.4, J8.4, J9.4, J10.4, J11.4, J12.4, J13.4, J14.4, J15.4, J16.4, U2.14 (VSS), U2.25 (EXTCLK), U3.6 (VSS), U3.29 (EP); also elsewhere on the board
unnamed: R4.2, U3.15 (INTB)
unnamed: R5.2, U3.16 (INTA)
unnamed: R6.2, U3.14 (~RESET)
unnamed: RN1.1 (R1.1), U2.9 (LED3)
unnamed: RN1.2 (R2.1), U2.8 (LED2)
unnamed: RN1.3 (R3.1), U2.7 (LED1)
unnamed: RN1.4 (R4.1), U2.6 (LED0)
unnamed: RN2.1 (R1.1), U2.13 (LED7)
unnamed: RN2.2 (R2.1), U2.12 (LED6)
unnamed: RN2.3 (R3.1), U2.11 (LED5)
unnamed: RN2.4 (R4.1), U2.10 (LED4)
unnamed: RN3.1 (R1.1), U2.18 (LED11)
unnamed: RN3.2 (R2.1), U2.17 (LED10)
unnamed: RN3.3 (R3.1), U2.16 (LED9)
unnamed: RN3.4 (R4.1), U2.15 (LED8)
unnamed: RN4.1 (R1.1), U2.22 (LED15)
unnamed: RN4.2 (R2.1), U2.21 (LED14)
unnamed: RN4.3 (R3.1), U2.20 (LED13)
unnamed: RN4.4 (R4.1), U2.19 (LED12)
unnamed: R15.2, U2.1 (A0)
unnamed: R16.2, U2.2 (A1)
unnamed: R3.2, U2.23 (~OE)
unnamed: R18.2, U3.11 (A0)
unnamed: R17.2, U3.12 (A1)

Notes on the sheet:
DNP
MCP23017 0x20
PCA9685 0x40

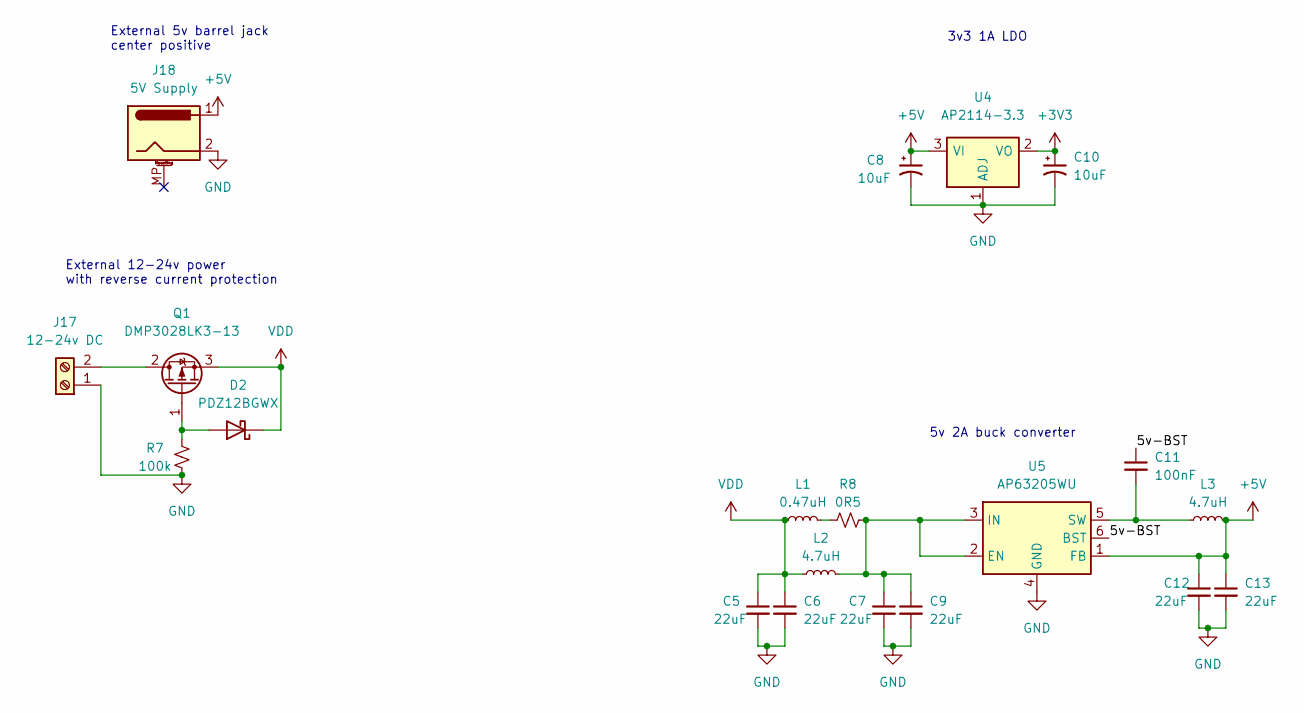
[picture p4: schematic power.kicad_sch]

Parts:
C5, C6, C9, C12, C13: 22uF; C_0603_1608Metric_Pad1.08x0.95mm_HandSolder; Mouser 810-C1608X5R0J226M
C7: 22uF; C_0603_1608Metric_Pad1.08x0.95mm_HandSolder; Mouser 810-C1608X5R0J226
C8, C10: 10uF; CP_Elec_5x5.3; Mouser 710-865230542002
C11: 100nF; C_0603_1608Metric_Pad1.08x0.95mm_HandSolder; Mouser 603-CC603KPX7R9BB104
D2: PDZ12BGWX; D_SOD-123; Mouser 771-PDZ12BGWX
J17: 12-24v DC; TerminalBlock_Phoenix_MKDS-1,5-2-5.08_1x02_P5.08mm_Horizont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; Mouser 649-220316-H021B01LF
J18: 5V Supply; BarrelJack_Horizontal
L1: 0.47uH; L_0603_1608Metric_Pad1.05x0.95mm_HandSolder; Mouser 810-MLZ1608DR47DT000
L2, L3: 4.7uH; L_Taiyo-Yuden_NR-40xx_HandSoldering; Mouser 963-NRS4018T4R7MDGJ
Q1: DMP3028LK3-13; TO-252-2; Mouser 621-DMP3028LK3-13
R7: 100k; R_1206_3216Metric_Pad1.30x1.75mm_HandSolder; Mouser 71-CRCW1206100KFKEAC
R8: 0R5; R_0805_2012Metric_Pad1.20x1.40mm_HandSolder; Mouser 756-LRCS0805-R50FT5
U4: AP2114-3.3; SOT-223-3_TabPin2; Mouser 621-AP2114H-3.3TRG1
U5: AP63205WU; TSOT-23-6; Mouser 621-AP63205WU-7

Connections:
+3V3: C10.1, U4.2 (VO); also elsewhere on the board
+5V: C8.1, C12.1, C13.1, J18.1, L3.2, U4.3 (VI), U5.1 (FB); also elsewhere on the board
/Power/5v-BST: C11.1, U5.6 (BST)
GND: C5.2, C6.2, C7.2, C8.2, C9.2, C10.2, C12.2, C13.2, J17.1, J18.2, R7.1, U4.1 (ADJ), U5.4 (GND); also elsewhere on the board
unnamed: C7.1, C9.1, L2.2, R8.2, U5.2 (EN), U5.3 (IN)
unnamed: C11.2, L3.1, U5.5 (SW)
unnamed: D2.2 (A), Q1.1 (G), R7.2
unnamed: J17.2, Q1.2 (D)
unnamed: L1.2, R8.1
VDD: C5.1, C6.1, D2.1 (K), L1.1, L2.1, Q1.3 (S)

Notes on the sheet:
5v 2A buck converter
External 12-24v power with reverse current protection
3v3 1A LDO
External 5v barrel jack center positive

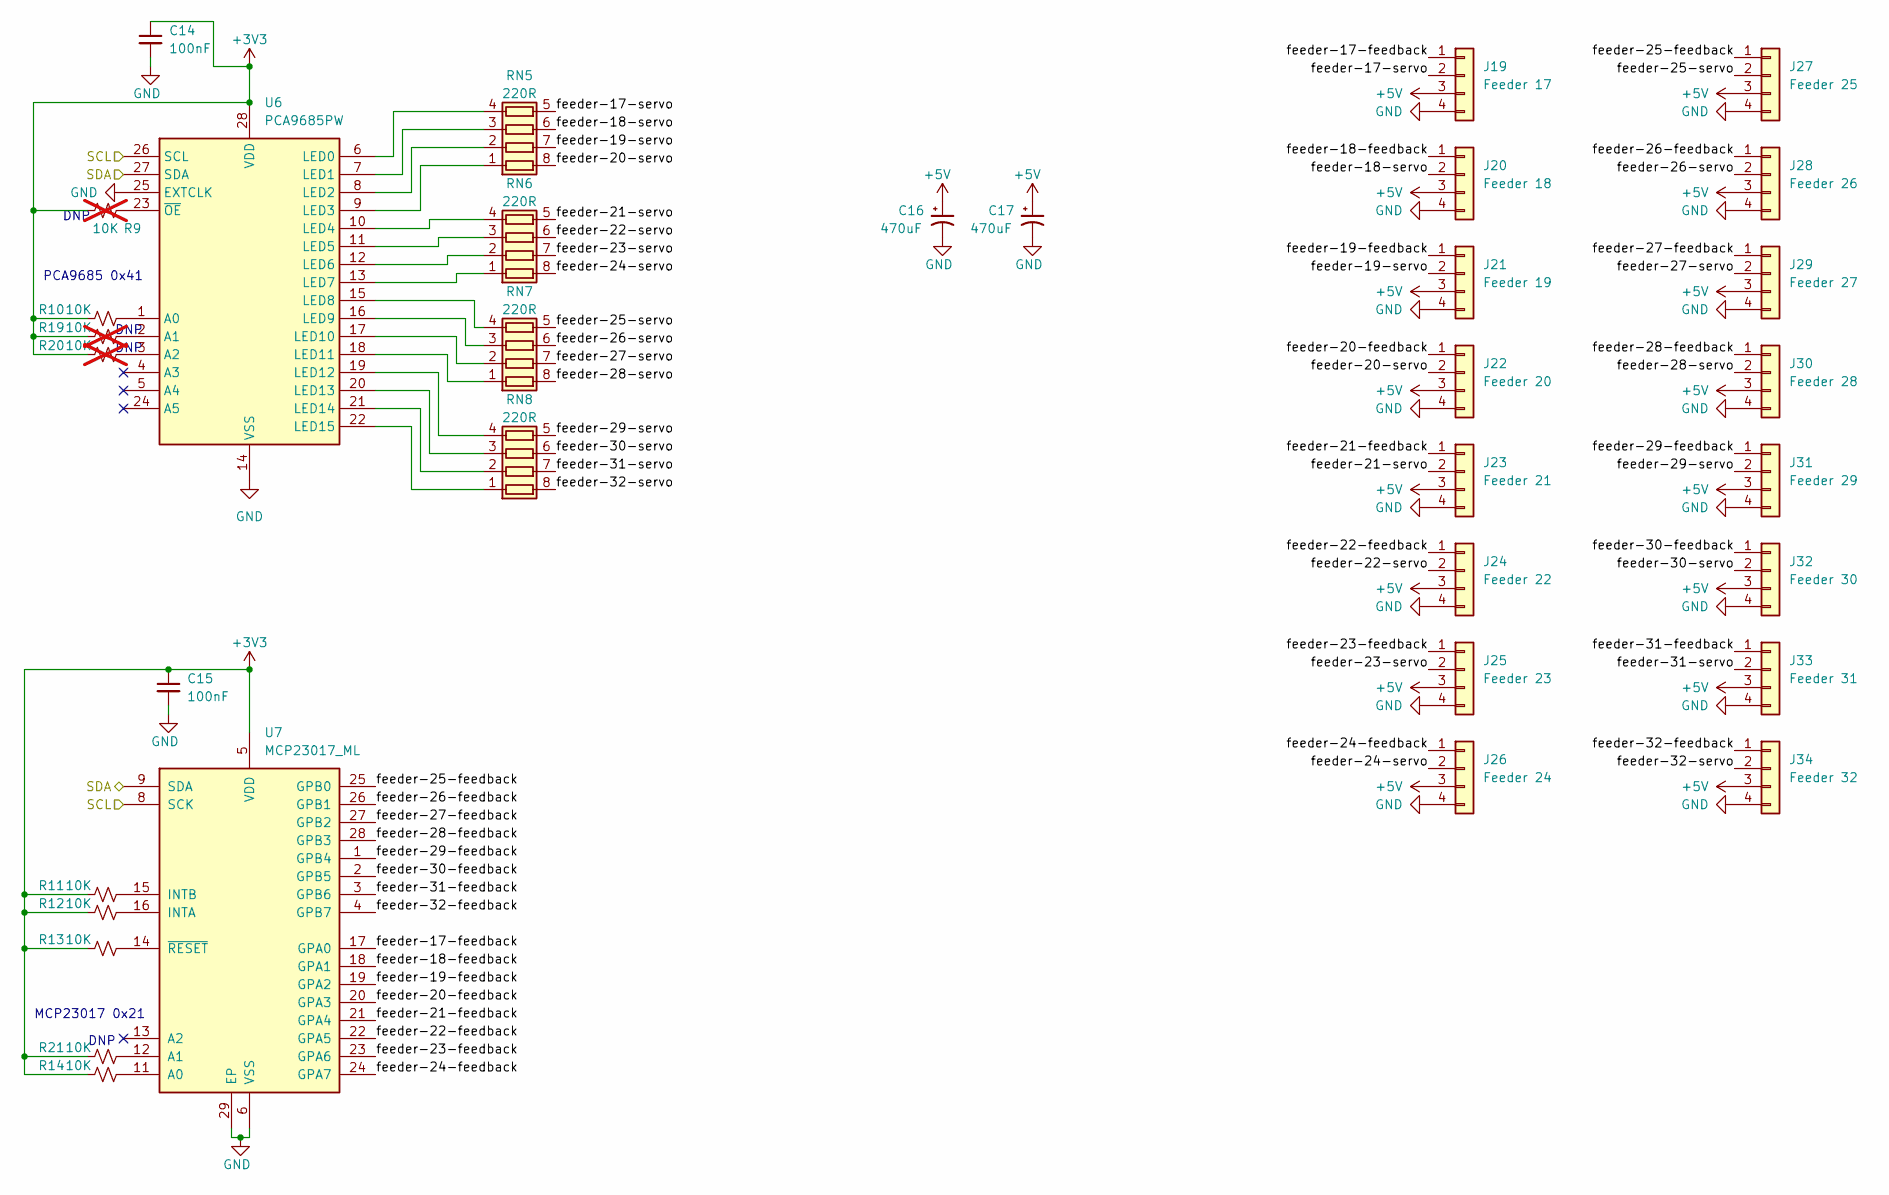
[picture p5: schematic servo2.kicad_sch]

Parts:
C14: 100nF; C_0603_1608Metric_Pad1.08x0.95mm_HandSolder
C15: 100nF; C_0603_1608Metric_Pad1.08x0.95mm_HandSolder; Mouser 791-0603B822K250CT
C16, C17: 470uF; CP_Radial_D8.0mm_P5.00mm
J19: Feeder 17; PinHeader_1x04_P2.54mm_Vertical
J20: Feeder 18; PinHeader_1x04_P2.54mm_Vertical
J21: Feeder 19; PinHeader_1x04_P2.54mm_Vertical
J22: Feeder 20; PinHeader_1x04_P2.54mm_Vertical
J23: Feeder 21; PinHeader_1x04_P2.54mm_Vertical
J24: Feeder 22; PinHeader_1x04_P2.54mm_Vertical
J25: Feeder 23; PinHeader_1x04_P2.54mm_Vertical
J26: Feeder 24; PinHeader_1x04_P2.54mm_Vertical
J27: Feeder 25; PinHeader_1x04_P2.54mm_Vertical
J28: Feeder 26; PinHeader_1x04_P2.54mm_Vertical
J29: Feeder 27; PinHeader_1x04_P2.54mm_Vertical
J30: Feeder 28; PinHeader_1x04_P2.54mm_Vertical
J31: Feeder 29; PinHeader_1x04_P2.54mm_Vertical
J32: Feeder 30; PinHeader_1x04_P2.54mm_Vertical
J33: Feeder 31; PinHeader_1x04_P2.54mm_Vertical
J34: Feeder 32; PinHeader_1x04_P2.54mm_Vertical
R9, R19, R20: 10K; R_0603_1608Metric_Pad0.98x0.95mm_HandSolder; Mouser 279-CRGCQ0603F10K; not fitted
R10, R11, R12, R13, R14, R21: 10K; R_0603_1608Metric_Pad0.98x0.95mm_HandSolder; Mouser 279-CRGCQ0603F10K
RN5, RN6, RN7, RN8: 220R; R_Array_Concave_4x0402
U6: PCA9685PW; TSSOP-28_4.4x9.7mm_P0.65mm
U7: MCP23017_ML; QFN-28-1EP_6x6mm_P0.65mm_EP4.25x4.25mm

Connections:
+3V3: C14.1, C15.1, R9.1, R10.1, R11.1, R12.1, R13.1, R14.1, R19.1, R20.1, R21.1, U6.28 (VDD), U7.5 (VDD); also elsewhere on the board
+5V: C16.1, C17.1, J19.3, J20.3, J21.3, J22.3, J23.3, J24.3, J25.3, J26.3, J27.3, J28.3, J29.3, J30.3, J31.3, J32.3, J33.3, J34.3; also elsewhere on the board
/SCL: U6.26 (SCL), U7.8 (SCK); also elsewhere on the board
/SDA: U6.27 (SDA), U7.9 (SDA); also elsewhere on the board
/ServoControl (17-32)/feeder-17-feedback: J19.1, U7.17 (GPA0)
/ServoControl (17-32)/feeder-17-servo: J19.2, RN5.5 (R4.2)
/ServoControl (17-32)/feeder-18-feedback: J20.1, U7.18 (GPA1)
/ServoControl (17-32)/feeder-18-servo: J20.2, RN5.6 (R3.2)
/ServoControl (17-32)/feeder-19-feedback: J21.1, U7.19 (GPA2)
/ServoControl (17-32)/feeder-19-servo: J21.2, RN5.7 (R2.2)
/ServoControl (17-32)/feeder-20-feedback: J22.1, U7.20 (GPA3)
/ServoControl (17-32)/feeder-20-servo: J22.2, RN5.8 (R1.2)
/ServoControl (17-32)/feeder-21-feedback: J23.1, U7.21 (GPA4)
/ServoControl (17-32)/feeder-21-servo: J23.2, RN6.5 (R4.2)
/ServoControl (17-32)/feeder-22-feedback: J24.1, U7.22 (GPA5)
/ServoControl (17-32)/feeder-22-servo: J24.2, RN6.6 (R3.2)
/ServoControl (17-32)/feeder-23-feedback: J25.1, U7.23 (GPA6)
/ServoControl (17-32)/feeder-23-servo: J25.2, RN6.7 (R2.2)
/ServoControl (17-32)/feeder-24-feedback: J26.1, U7.24 (GPA7)
/ServoControl (17-32)/feeder-24-servo: J26.2, RN6.8 (R1.2)
/ServoControl (17-32)/feeder-25-feedback: J27.1, U7.25 (GPB0)
/ServoControl (17-32)/feeder-25-servo: J27.2, RN7.5 (R4.2)
/ServoControl (17-32)/feeder-26-feedback: J28.1, U7.26 (GPB1)
/ServoControl (17-32)/feeder-26-servo: J28.2, RN7.6 (R3.2)
/ServoControl (17-32)/feeder-27-feedback: J29.1, U7.27 (GPB2)
/ServoControl (17-32)/feeder-27-servo: J29.2, RN7.7 (R2.2)
/ServoControl (17-32)/feeder-28-feedback: J30.1, U7.28 (GPB3)
/ServoControl (17-32)/feeder-28-servo: J30.2, RN7.8 (R1.2)
/ServoControl (17-32)/feeder-29-feedback: J31.1, U7.1 (GPB4)
/ServoControl (17-32)/feeder-29-servo: J31.2, RN8.5 (R4.2)
/ServoControl (17-32)/feeder-30-feedback: J32.1, U7.2 (GPB5)
/ServoControl (17-32)/feeder-30-servo: J32.2, RN8.6 (R3.2)
/ServoControl (17-32)/feeder-31-feedback: J33.1, U7.3 (GPB6)
/ServoControl (17-32)/feeder-31-servo: J33.2, RN8.7 (R2.2)
/ServoControl (17-32)/feeder-32-feedback: J34.1, U7.4 (GPB7)
/ServoControl (17-32)/feeder-32-servo: J34.2, RN8.8 (R1.2)
GND: C14.2, C15.2, C16.2, C17.2, J19.4, J20.4, J21.4, J22.4, J23.4, J24.4, J25.4, J26.4, J27.4, J28.4, J29.4, J30.4, J31.4, J32.4, J33.4, J34.4, U6.14 (VSS), U6.25 (EXTCLK), U7.6 (VSS), U7.29 (EP); also elsewhere on the board
unnamed: R9.2, U6.23 (~OE)
unnamed: R10.2, U6.1 (A0)
unnamed: R11.2, U7.15 (INTB)
unnamed: R12.2, U7.16 (INTA)
unnamed: R13.2, U7.14 (~RESET)
unnamed: R14.2, U7.11 (A0)
unnamed: RN5.1 (R1.1), U6.9 (LED3)
unnamed: RN5.2 (R2.1), U6.8 (LED2)
unnamed: RN5.3 (R3.1), U6.7 (LED1)
unnamed: RN5.4 (R4.1), U6.6 (LED0)
unnamed: RN6.1 (R1.1), U6.13 (LED7)
unnamed: RN6.2 (R2.1), U6.12 (LED6)
unnamed: RN6.3 (R3.1), U6.11 (LED5)
unnamed: RN6.4 (R4.1), U6.10 (LED4)
unnamed: RN7.1 (R1.1), U6.18 (LED11)
unnamed: RN7.2 (R2.1), U6.17 (LED10)
unnamed: RN7.3 (R3.1), U6.16 (LED9)
unnamed: RN7.4 (R4.1), U6.15 (LED8)
unnamed: RN8.1 (R1.1), U6.22 (LED15)
unnamed: RN8.2 (R2.1), U6.21 (LED14)
unnamed: RN8.3 (R3.1), U6.20 (LED13)
unnamed: RN8.4 (R4.1), U6.19 (LED12)
unnamed: R19.2, U6.2 (A1)
unnamed: R20.2, U6.3 (A2)
unnamed: R21.2, U7.12 (A1)

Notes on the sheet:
DNP
MCP23017 0x21
PCA9685 0x41

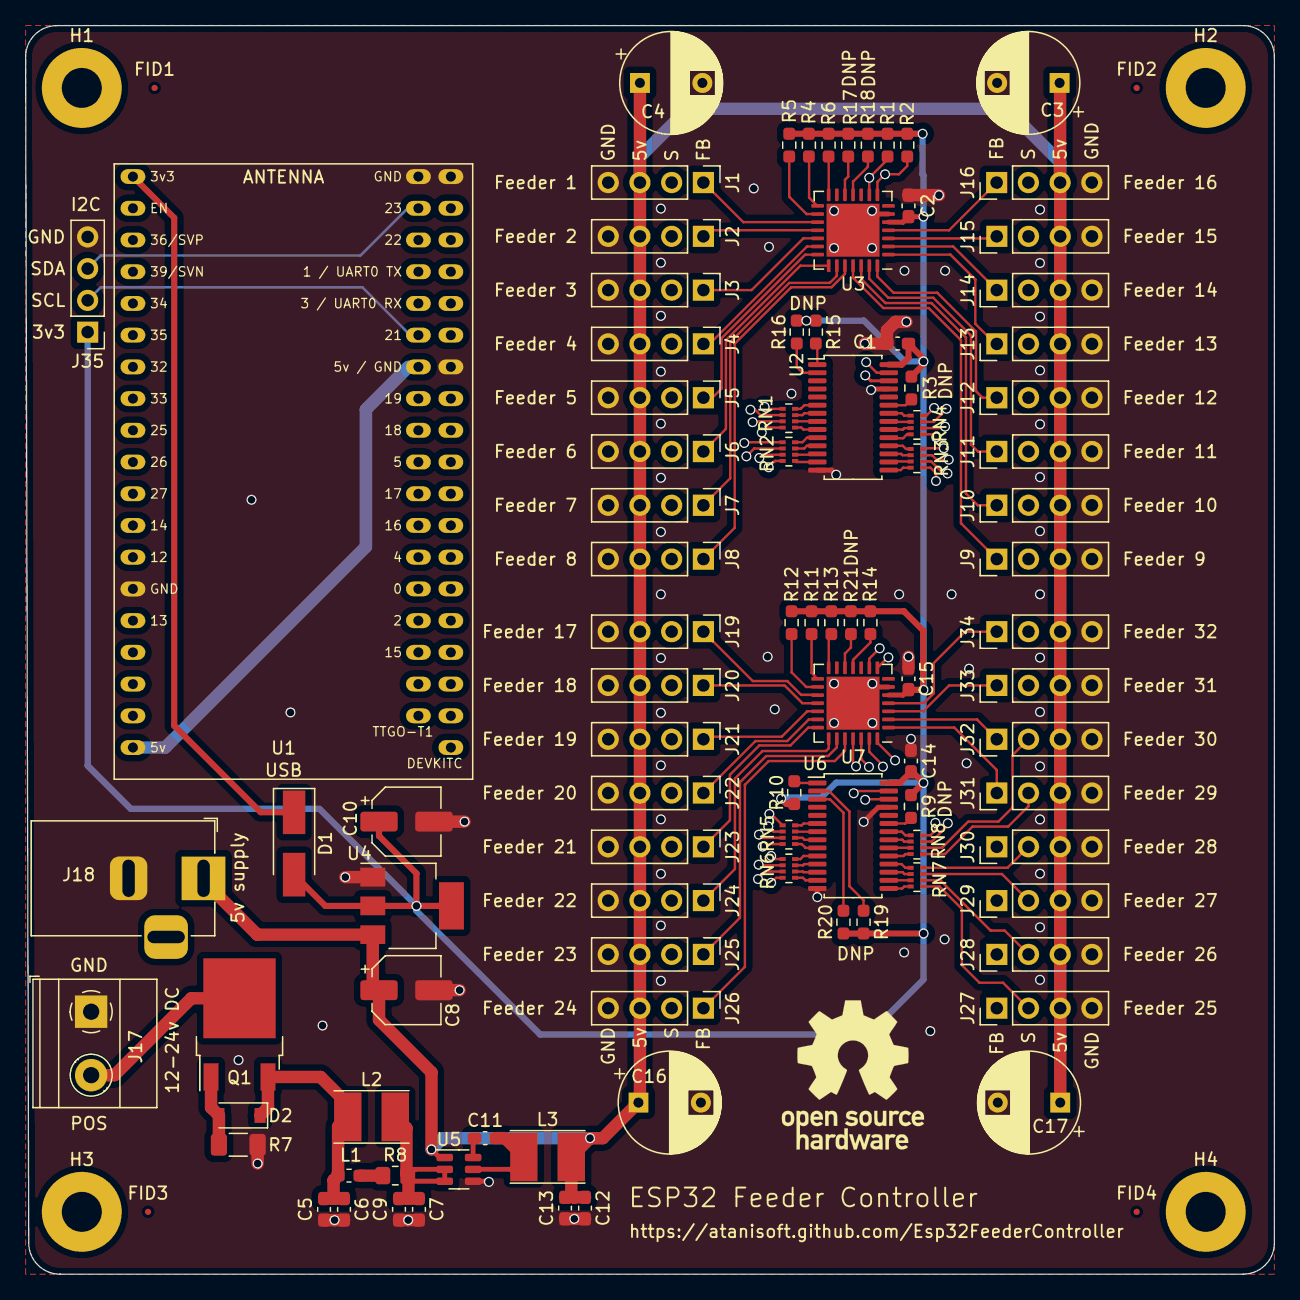
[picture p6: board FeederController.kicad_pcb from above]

Board: 4 copper layers, 100.0 x 100.0 mm, 102 parts (0 on the bottom side), 126 nets.

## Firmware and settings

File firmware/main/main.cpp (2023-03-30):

/*
 * SPDX-FileCopyrightText: 2022 Mike Dunston (atanisoft)
 *
 * SPDX-License-Identifier: CC-BY-NC-SA-4.0
 */

#include <algorithm>
#include <asio.hpp>
#include <esp_chip_info.h>
#include <esp_heap_caps.h>
#include <esp_log.h>
#include <esp_ota_ops.h>
#include <esp_pthread.h>
#include <nvs.h>
#include <nvs_flash.h>
#include <string>

#include "config.hxx"
#include "FeederManager.hxx"
#include "WiFiManager.hxx"
#include "GCodeServer.hxx"
#include "Utils.hxx"
#include "SocInfo.hxx"

// Compile time validation of configuration parameters
static_assert(__builtin_strlen(WIFI_SSID) > 0,
              "WiFi SSID must not be blank");
static_assert(__builtin_strlen(WIFI_HOSTNAME) < 32,
              "Hostname length must not exceed 32 characters");

static WiFiManager wifi(WIFI_SSID, WIFI_PASSWORD, WIFI_HOSTNAME);

static void worker_task(asio::io_context &context)
{
    const char *const TAG = "worker";
    try
    {
        context.run();
    }
    catch (const std::exception &e)
    {
        ESP_LOGE(TAG, "Exception occured during client thread execution %s",
                 e.what());
    }
    catch (...)
    {
        ESP_LOGE(TAG, "Unknown exception");
    }
}

extern "C"
{

/*
workaround for:
xtensa-esp32-elf/bin/ld: esp-idf/espressif__asio/libespressif__asio.a(asio.cpp.obj):(.literal._ZN4asio6detail10socket_ops9inet_ntopEiPKvPcjmRSt10error_code+0x8): undefined reference to `if_indextoname'
xtensa-esp32-elf/bin/ld: esp-idf/espressif__asio/libespressif__asio.a(asio.cpp.obj): in function `_ZN4asio6detail10socket_ops9inet_ntopEiPKvPcjmRSt10error_code':
Esp32FeederController/firmware/managed_components/espressif__asio/asio/asio/include/asio/detail/impl/socket_ops.ipp:2128: undefined reference to `if_indextoname'
collect2: error: ld returned 1 exit status

Per https://github.com/espressif/esp-idf/issues/3557 this should have been
fixed but it appears to be showing up on IDF v5.x with external asio component.
*/
__attribute__((weak)) char* if_indextoname(unsigned int, char*) { return 0; }

void app_main()
{
    const esp_app_desc_t *app_data = esp_app_get_description();
    const esp_partition_t *running_from = esp_ota_get_running_partition();
    const char *const TAG = "main";
    esp_chip_info_t chip_info;

    esp_chip_info(&chip_info);
    configure_log_levels();

    ESP_LOGI(TAG, "%s %s Initializing", app_data->project_name, app_data->version);
    ESP_LOGI(TAG, "Compiled on %s %s using IDF %s", app_data->date,
             app_data->time, app_data->idf_ver);
    ESP_LOGI(TAG, "Running from: %s", running_from->label);
    SocInfo::print_soc_info();

    // Initialize NVS before we do any other initialization as it may be
    // internally used by various components even if we disable it's usage in
    // the WiFi connection stack.
    ESP_LOGI(TAG, "Initializing NVS");
    if (ESP_ERROR_CHECK_WITHOUT_ABORT(nvs_flash_init()) == ESP_ERR_NVS_NO_FREE_PAGES)
    {
        const esp_partition_t *partition =
            esp_partition_find_first(ESP_PARTITION_TYPE_DATA,
                                     ESP_PARTITION_SUBTYPE_DATA_NVS, NULL);
        if (partition != NULL)
        {
            ESP_LOGI(TAG, "Erasing partition %s...", partition->label);
            ESP_ERROR_CHECK(esp_partition_erase_range(partition, 0, partition->size));
            ESP_ERROR_CHECK(nvs_flash_init());
        }
    }

    if (!wifi.start())
    {
        ESP_LOGE(TAG, "Failed to connect to WiFi, rebooting");
        abort();
    }

    asio::io_context context;
    GCodeServer gcode_server(context, wifi.get_local_ip());
    FeederManager feeder_mgr(gcode_server, context);
    asio::system_timer heap_timer(context, std::chrono::seconds(30));
    std::function<void(asio::error_code)> heap_monitor =
        [&](asio::error_code ec)
    {
        const char *const HEAP_TAG = "heap_mon";
        if (!ec)
        {
            ESP_LOGI(HEAP_TAG, "Heap: %.2fkB / %.2fkB",
                     heap_caps_get_free_size(MALLOC_CAP_INTERNAL) / 1024.0f,
                     heap_caps_get_total_size(MALLOC_CAP_INTERNAL) / 1024.0f);
#if CONFIG_SPIRAM_SUPPORT
            ESP_LOGI(HEAP_TAG, "PSRAM: %.2fkB / %.2fkB",
                     heap_caps_get_free_size(MALLOC_CAP_SPIRAM) / 1024.0f,
                     heap_caps_get_total_size(MALLOC_CAP_SPIRAM) / 1024.0f);
#endif // CONFIG_SPIRAM_SUPPORT
            heap_timer.expires_from_now(std::chrono::seconds(30));
            heap_timer.async_wait(heap_monitor);
        }
    };

    // start the heap monitor task, this is necessary to kick start the task
    // in the background.
    heap_monitor({});

    std::vector<std::thread> workers;
    // Create two workers per core to increase concurrency of execution.
    const int worker_count = chip_info.cores * 2;
    ESP_LOGI(TAG, "Creating %d worker threads", worker_count);
    for (int id = 0; id < worker_count; id++)
    {
        // std::thread does not expose options for thread name, stack size or
        // pinning to a core. ESP-IDF provides a pthread extension for this
        // which must be called prior to thread creation.
        auto cfg = esp_pthread_get_default_config();
        std::string name = "worker-";
        name.append(std::to_string(id));
        cfg.thread_name = name.c_str();
        cfg.pin_to_core = id % 2;
        esp_pthread_set_cfg(&cfg);

        // Create the worker thread which passes in the asio::io_context by
        // reference. Internally the asio::io_context object will manage
        // locking as required.
        workers.emplace_back(std::thread(worker_task, std::ref(context)));
    }
    ESP_LOGI(TAG, "%s Ready!", app_data->project_name);

    // Wait for all workers to exit.
    for (auto &worker : workers)
    {
        worker.join();
    }
}

} // extern "C"

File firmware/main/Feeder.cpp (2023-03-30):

/*
 * SPDX-FileCopyrightText: 2022 Mike Dunston (atanisoft)
 *
 * SPDX-License-Identifier: CC-BY-NC-SA-4.0
 */

#include <asio.hpp>
#include <esp_log.h>
#include <cstdint>
#include <nvs.h>
#include <nvs_flash.h>
#include <string>

#include "config.hxx"
#include "GCodeServer.hxx"
#include "FeederManager.hxx"
#include "Feeder.hxx"
#include "Utils.hxx"

Feeder::Feeder(std::size_t id, uint32_t uuid, std::shared_ptr<PCA9685> pca9685,
           uint8_t channel, asio::io_context &context,
           std::shared_ptr<MCP23017> mcp23017)
    : id_(id), uuid_(uuid), pca9685_(pca9685), mcp23017_(mcp23017),
      channel_(channel), timer_(context)
{
    nvskey_ = "feeder-";
    nvskey_.append(to_hex(uuid_));
}

bool Feeder::move(uint8_t distance)
{
    const std::lock_guard<std::mutex> lock(mux_);
    if (is_moving())
    {
        ESP_LOGW(TAG,
                 "[%s:%zu] Feeder is already in motion, rejecting move.",
                 to_hex(uuid_).c_str(), id_);
        return false;
    }

    if (distance == 0)
    {
        movement_ = config_.feed_length;
    }
    else
    {
        movement_ = distance;
    }

    status_ = FEEDER_MOVING;

    // start moving the feeder forward.
    move_locked();

    return true;
}

bool Feeder::post_pick()
{
    if (!is_enabled())
    {
        return false;
    }
    else if (position_ != POSITION_RETRACTED)
    {
        const std::lock_guard<std::mutex> lock(mux_);
        retract_locked();
    }
    return true;
}

std::string Feeder::status()
{
    std::string status = FeederManager::FEEDER_STATUS_CMD;
    status.reserve(128);
    status.append(" N").append(std::to_string(id_));
    status.append(" A").append(std::to_string(config_.servo_full_angle));
    status.append(" B").append(std::to_string(config_.servo_half_angle));
    status.append(" C").append(std::to_string(config_.servo_retract_angle));
    status.append(" D").append(std::to_string(config_.movement_degrees));
    status.append(" F").append(std::to_string(config_.feed_length));
    status.append(" S").append(std::to_string(config_.movement_interval_ms));
    status.append(" U").append(std::to_string(config_.settle_time_ms));
    status.append(" V").append(std::to_string(config_.servo_min_pulse));
    status.append(" W").append(std::to_string(config_.servo_max_pulse));
    status.append(" X").append(std::to_string(position_));
    status.append(" Y").append(std::to_string(status_));
    status.append(" Z").append(std::to_string(config_.ignore_feedback));
    return status;
}

bool Feeder::enable()
{
    const std::lock_guard<std::mutex> lock(mux_);
    status_ = FEEDER_IDLE;
    return true;
}

bool Feeder::disable()
{
    const std::lock_guard<std::mutex> lock(mux_);
    status_ = FEEDER_DISABLED;
    return true;
}

void Feeder::configure(uint8_t advance_angle, uint8_t half_advance_angle,
                       uint8_t retract_angle, uint8_t feed_length,
                       uint16_t settle_time_ms, uint8_t min_pulse,
                       uint8_t max_pulse, int8_t ignore_feedback,
                       int16_t movement_speed_ms, uint8_t movement_degrees)
{
    bool need_persist = false;
    if (advance_angle)
    {
        config_.servo_full_angle = advance_angle;
        need_persist = true;
    }
    if (half_advance_angle)
    {
        config_.servo_half_angle = half_advance_angle;
        need_persist = true;
    }
    if (retract_angle)
    {
        config_.servo_retract_angle = retract_angle;
        need_persist = true;
    }
    if (feed_length)
    {
        if ((feed_length % 2) == 0)
        {
            config_.feed_length = feed_length;
            need_persist = true;
        }
    }
    if (settle_time_ms)
    {
        config_.settle_time_ms = settle_time_ms;
        need_persist = true;
    }
    if (min_pulse)
    {
        config_.servo_min_pulse = min_pulse;
        need_persist = true;
    }
    if (ignore_feedback >= 0)
    {
        config_.ignore_feedback = ignore_feedback;
        need_persist = true;
    }
    if (movement_speed_ms >= 0)
    {
        config_.movement_interval_ms = movement_speed_ms;
        need_persist = true;
    }
    if (movement_degrees)
    {
        config_.movement_degrees = movement_degrees;
        need_persist = true;
    }

    if (need_persist)
    {
        nvs_handle_t nvs;
        // persist the updated configuration
        ESP_ERROR_CHECK(nvs_open(NVS_FEEDER_NAMESPACE, NVS_READWRITE, &nvs));
        ESP_ERROR_CHECK(
            nvs_set_blob(nvs, nvskey_.c_str(), &config_, configsize_));
        ESP_ERROR_CHECK(nvs_commit(nvs));
        nvs_close(nvs);
    }
}

bool Feeder::is_busy()
{
    return !is_enabled() && status_ != FEEDER_IDLE;
}

bool Feeder::is_enabled()
{
    return status_ != FEEDER_DISABLED;
}

bool Feeder::is_moving()
{
    return status_ == FEEDER_MOVING;
}

bool Feeder::is_tensioned()
{
    const std::lock_guard<std::mutex> lock(mux_);

    if (config_.ignore_feedback)
    {
        return true;
    }

    return tensioned_;
}

void Feeder::feedback_state_changed(bool state)
{
    {
        const std::lock_guard<std::mutex> lock(mux_);
        tensioned_ = state;
    }

    // If the feeder is not currently busy check the state of the feedback to
    // see if a manual advancement has been requested by pressing the tape
    // tensioning arm down for ~50ms before releasing.
    if (!is_busy())
    {
        if (!tensioned_)
        {
            advance_ = true;
        }
        else if (advance_)
        {
            move();
            advance_ = false;
        }
    }
    else
    {
        advance_ = false;
    }
}
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

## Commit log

2022-03-18 Add periodic timer for heap monitoring. Moved feeder management code to FeederManager.hxx Added SocInfo during startup.
2022-03-19 Adding servo movement control and initial implementation of retract/move.
2022-03-22 Split/rework Feeder integration to include a timer per feeder
    [Feeder.cpp, FeederManager.cpp, main.cpp]
2022-03-23 Integrate MCP23017 for feeder feedback.
    Shifted SCL from 22 to 21 (TTGO-T1 uses 22 for on-board LED).
2022-03-24 Add initial PCB, not yet tested
    [FeederController.kicad_pcb, FeederController.kicad_sch, power.kicad_sch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]
2022-03-24 add correct pcb render
2022-03-25 Update PCB as below
    * Adjusted placement of mounting holes to line up with LumenPnP staging plate.
    * Added 2k4 P/U for SDA/SCL.
    * GND plane stitching
    [FeederController.kicad_pcb, FeederController.kicad_sch, power.kicad_sch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]
2022-03-25 Feeder servo control integration work.
    Feeders should now be able to advance/retract as expected when commands are received.
2022-03-26 Added a few DNP footprints for connecting two PCBs together using a single ESP32
    [FeederController.kicad_pcb, FeederController.kicad_sch, servo1.kicad_sch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]
2022-03-27 Initial re-creation of Feeder PCB using SMD diode and JST-PH connector for N20
    [Feeder-panel.kicad_pcb, Feeder.kicad_pcb, Feeder.kicad_sch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]
2022-03-27 Update Feeder PCB to adjust footprints for clearances.
    [Feeder-4x8-panel.kicad_pcb, Feeder-panel.kicad_pcb, Feeder.kicad_pcb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]
2022-03-29 Fix compilation errors and M115 output.
    [Feeder.cpp]
2022-04-09 Adding support for manual advance and slowing servo movement.
2022-05-22 Feeder - added optional THT diode footprint, repanelized (#1)
    * Feeder - added optional THT diode footprint, repanelized
    * Create IMPORTANT-ORDERING-INSTRUCTIONS.txt
    [Feeder-4x8-panel.kicad_pcb, Feeder-Panelized.kicad_pcb, Feeder.kicad_pcb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]
2022-05-25 re-panelized to use silk screen between small PCBs to reduce cost (#3)
    [Feeder-Panelized-Silkscreen.kicad_pcb]
2022-06-16 recreated feeder PCB for new 0816 CAD design (#5)
    [Feeder-Panelized-Silkscreen.kicad_pcb, Feeder-Panelized.kicad_pcb, Feeder.kicad_pcb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]
2022-07-12 Rearrange controller PCB files, removed Feeder PCB files
    [Feeder-Panelized.kicad_pcb, Feeder.kicad_pcb, Feeder.kicad_sch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]
2023-04-01 Fix off-by-one error in feeder numbering.
    Fixes: https://github.com/atanisoft/Esp32FeederController/issues/9
    [FeederManager.cpp]
2023-04-16 Exclude R3 and R9 from population.
    Upgrades files to KiCad 7.x.
    Fixes: https://github.com/atanisoft/Esp32FeederController/issues/10
    [FeederController.kicad_pcb, FeederController.kicad_sch, power.kicad_sch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]
